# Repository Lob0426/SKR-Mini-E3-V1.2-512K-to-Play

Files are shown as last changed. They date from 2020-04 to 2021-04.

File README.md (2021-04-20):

# SKR-Mini-E3-V1.2-512K-to-Play
SKR Mini E3 V1.2 firmware for Printrbot Play w/o heated Bed (12/20/20)
This Firmware is used at your own risk.
This is for a Printrbot Play without heated Bed and has 3 point leveling for the induction probe. It has features set such as S_CURVE, LIN_ADV and ARC support.
It is set for the default size of 102mm X 102mm X 131
The SKR Mini5.stl is the one I finally used. It is a printable adapter plate from printrboard to SKR MINI. It orients the board 90degrees to the original board position. It lines the MicrSD on the board with the SD port in the Play chassis. This allowed me to use a Stock "CR10" LCD display where you need to use the onboard SD card to load files. The recommended TFT displays have USB and SD ports on them so this is not necessary to do for them. For the TFT displays you can use SKR Mini3.stl, but if you want to update firmware you will have to find a way to get to the MicroSD onboard to carry out that update. I recommend using the SKR Mini5.stl!

Board:
The Bigtreetech SKR Mini E3 Mini V1.2 board This board was designed as a direct replacement part for the Creality Ender 3 series of 3D Printers. It's size and layout match the Creality 1.1.4 and Creality 1.1.5 boards plus add extra connectors for TFT, NEOPixel, Filament runout sensor, BLTouch (servo connector), and extra fans
Specifications: Size: 100mm * 70.25mm
ARM Cortex-M3 CPU @ 75Mhz 256Kb documented available Flash (512 undocumented), 48K RAM.
Voltage: 12v or 24V operation depending on PSU, Hotend and Heated Bed unit used.
Drivers: Integrated TMC2209 drivers UART mode
Motor drive interfaces: X Axis, Y Axis, Z Axis, Extruder 0 (single extruder board)
Temperature Sensor interface: TH0, THB, 2 channel 100K NTC (thermal resistance)
Displays supported: 2.8"TFT, 3.5"TFT, Ender 3 original (CR10 display) LCD 12864 display
PC Communication interface: Mini USB type B @ 115200baud
File format: G-code
Recommended software: CURA, Simplify3D, Pronterface, Repetier-host, Makerware.

1/5/21 Added a BTT TFT35 E3 V3.0 Touchscreen to the Play. This allows you to usea USB stick or a full size SD card print instead. Makes the Play a whole lot easier to use. But the adapter board allows you to also use the Bords MicroSD card as well.

Connectors:
Connector type; JST-XH 2.54mm : Example: JST-XH connector set on Amazon
The Connectors on Printrbots are Molex(white) and Dupont(Black). To switch over to the SKR boards these have to be replaced or adapted to JST-XH connectors.
The Adaptrboard set adapts the Printrbot connectors to the SKR. They are a set of boards with incoming and outgoing terminals. The outgoing side plugs in from the Printrbot appropriate components plugs (X axis, Y axis, Z axis, Hotend etc.). The incoming side is to the SKR board you chose. The incoming side has short extensions (100mm about 4") between the SKR board and the Adaptrboards.
Manually replace the Molex and Dupont connectors with JST-XH connectors by cutting, stripping and crimping wires. 27 to 29 (1 fan, the hotend and the heated bed go into screw block and just need cutting and stripping) wires depending on whether you have a heated bed or not. Plus more if you have LEDS, NEOPixel, extra switches.
Another method would be to buy JST-XH 2.54mm Male wired cable connectors. Then cut, strip and solder and cover with shrink tube. This is probably as time consuming as crimping in the end. For some this is easier than crimping all those small pins to wires.

Of all these methods the cheapest is to crimp your own, the easiest is to buy the Adaptrboards and the most expensive is to solder them up. The Adaptrboards also have the advantage in they address the induction probe without having to wire in additional components. But if you are in a hurry and want to upgrade now, these are your options.

The Play Probe mount "Play probe mount18mm6.stl" (added 1/13/21) is for an 18mm inductive probe. The 8mm detection distance allows you to use a Ender 3/5 style magnetic removeable bed. This allows you to get rid of the Blue tape or PEI sheet. I finished the mount and it was flipped over to grab farther up the probe for a better grip. The earlier versions were allowing the probe to slip up and cause hotend crashes and melting pits in the build surface. This mount allows the probe to fit under the stock hotend cover.

printrbot foot2.stl is taller foot pads printed from TPU to improve cooling.

Overall the Play conversion has made it easier to use, easier to adjust and way quieter. It is what we see in Modern 3D printers produced today. It also has added safety as it has thermal overrun protection and resume after power outage. 

For more information see the Wiki: https://github.com/Lob0426/SKR-Mini-E3-V1.2-512K-to-Play/wiki

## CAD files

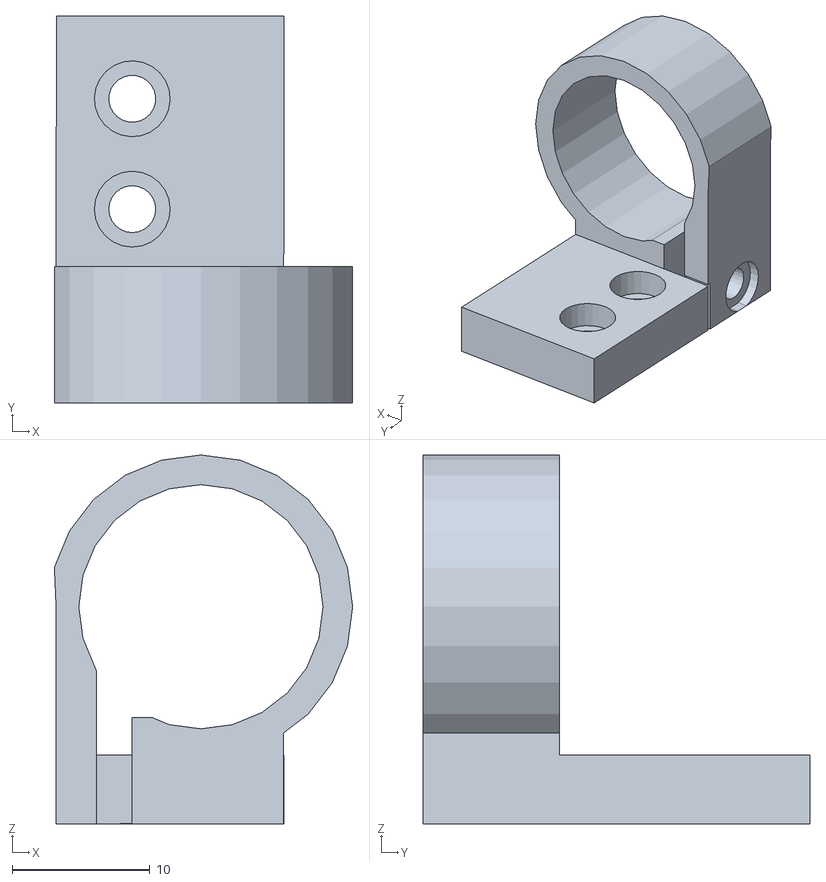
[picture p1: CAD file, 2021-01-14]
Play probe mount 18mm6.stl
21.6 x 28.1 x 26.8

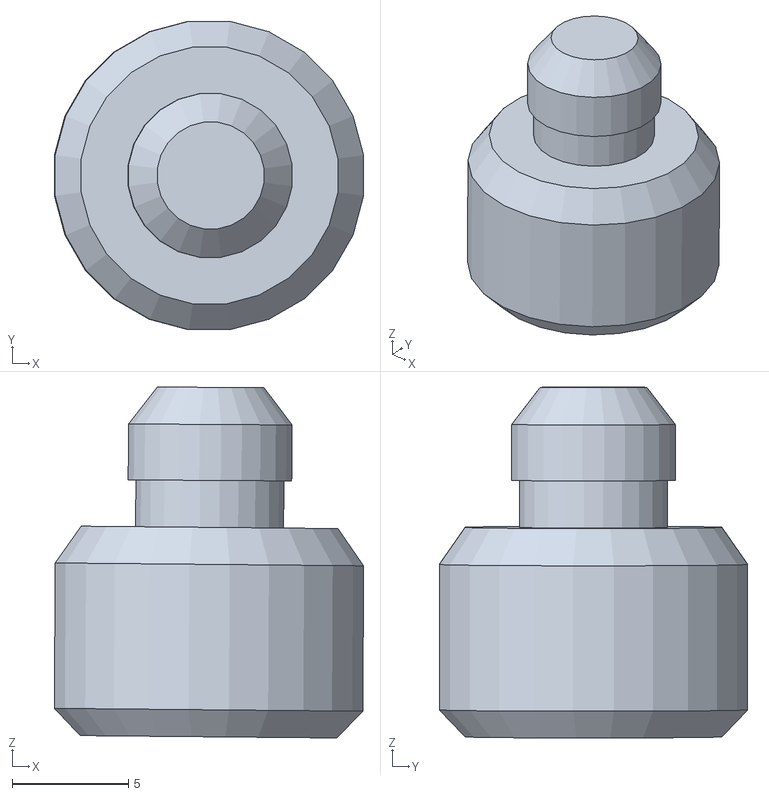
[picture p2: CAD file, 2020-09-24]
printrbot foot2.stl
13.3 x 13.3 x 15.1

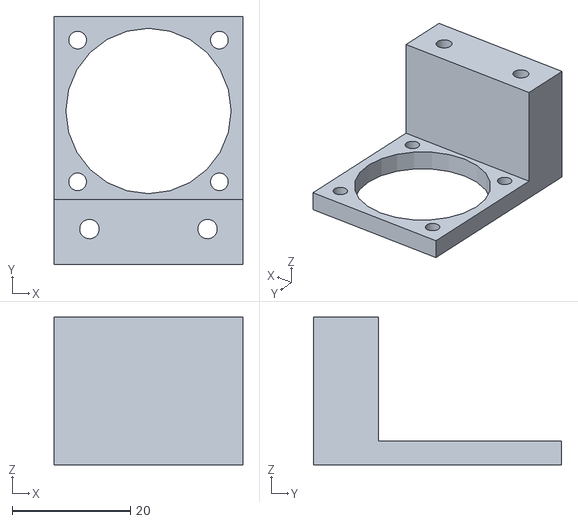
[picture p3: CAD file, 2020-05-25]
SKR fan mount2.stl
32.0 x 42.0 x 25.0

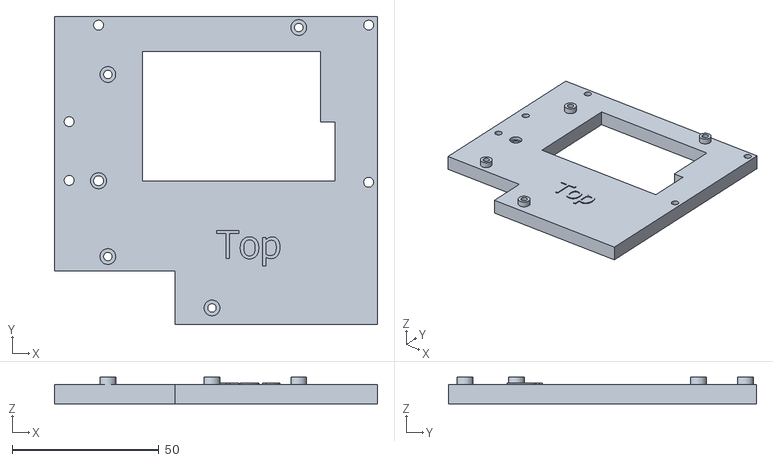
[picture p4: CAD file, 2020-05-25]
printrboard to SKR Mini5.stl
110.0 x 105.0 x 9.19

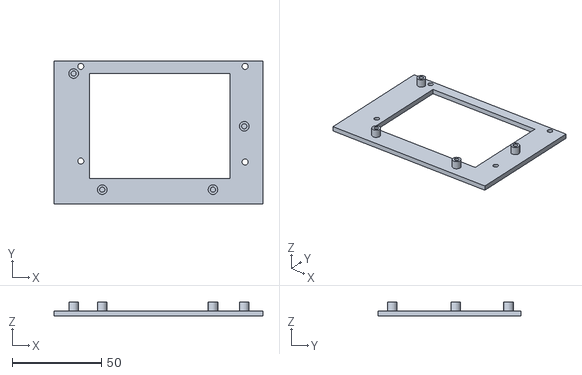
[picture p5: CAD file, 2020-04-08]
printrboard to SKR Mini3.stl
117.0 x 80.0 x 8.00

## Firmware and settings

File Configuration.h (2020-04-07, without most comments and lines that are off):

#pragma once
#define CONFIGURATION_H_VERSION 020000
#define STRING_CONFIG_H_AUTHOR "(BIGTREETECH, SKR-mini-E3-V1.2)" // Who made the changes.
#define SHOW_BOOTSCREEN
#define SERIAL_PORT 2
#define SERIAL_PORT_2 -1
#define BAUDRATE 115200
  #define MOTHERBOARD BOARD_BTT_SKR_MINI_E3_V1_2
#define CUSTOM_MACHINE_NAME "Printrbot Play"
#define EXTRUDERS 1
#define DEFAULT_NOMINAL_FILAMENT_DIA 1.75
#define TEMP_SENSOR_0 1
#define TEMP_SENSOR_1 0
#define TEMP_SENSOR_2 0
#define TEMP_SENSOR_3 0
#define TEMP_SENSOR_4 0
#define TEMP_SENSOR_5 0
#define TEMP_SENSOR_BED 5
#define TEMP_SENSOR_CHAMBER 0
#define DUMMY_THERMISTOR_998_VALUE 25
#define DUMMY_THERMISTOR_999_VALUE 100
#define MAX_REDUNDANT_TEMP_SENSOR_DIFF 10
#define TEMP_RESIDENCY_TIME     10  // (seconds) Time to wait for hotend to "settle" in M109
#define TEMP_WINDOW              1  // (°C) Temperature proximity for the "temperature reached" timer
#define TEMP_HYSTERESIS          3  // (°C) Temperature proximity considered "close enough" to the target
#define TEMP_BED_RESIDENCY_TIME 10  // (seconds) Time to wait for bed to "settle" in M190
#define TEMP_BED_WINDOW          1  // (°C) Temperature proximity for the "temperature reached" timer
#define TEMP_BED_HYSTERESIS      5  // (°C) Temperature proximity considered "close enough" to the target
#define HEATER_0_MINTEMP   3
#define HEATER_1_MINTEMP   5
#define HEATER_2_MINTEMP   5
#define HEATER_3_MINTEMP   5
#define HEATER_4_MINTEMP   5
#define HEATER_5_MINTEMP   5
#define BED_MINTEMP        3
#define HEATER_0_MAXTEMP 255
#define HEATER_1_MAXTEMP 275
#define HEATER_2_MAXTEMP 275
#define HEATER_3_MAXTEMP 275
#define HEATER_4_MAXTEMP 275
#define HEATER_5_MAXTEMP 275
#define BED_MAXTEMP      105
#define PIDTEMP
#define BANG_MAX 255     // Limits current to nozzle while in bang-bang mode; 255=full current
#define PID_MAX BANG_MAX // Limits current to nozzle while PID is active (see PID_FUNCTIONAL_RANGE below); 255=full current
#define PID_K1 0.95      // Smoothing factor within any PID loop
  #define PID_FUNCTIONAL_RANGE 10 // If the temperature difference between the target temperature and the actual temperature
  #define DEFAULT_Kp 40.15
  #define DEFAULT_Ki 7.10
  #define DEFAULT_Kd 56.73
#define MAX_BED_POWER 255 // limits duty cycle to bed; 255=full current
#define PREVENT_COLD_EXTRUSION
#define EXTRUDE_MINTEMP 170
#define PREVENT_LENGTHY_EXTRUDE
#define EXTRUDE_MAXLENGTH 600
#define THERMAL_PROTECTION_HOTENDS // Enable thermal protection for all extruders
#define THERMAL_PROTECTION_BED     // Enable thermal protection for the heated bed
#define THERMAL_PROTECTION_CHAMBER // Enable thermal protection for the heated chamber
#define USE_XMIN_PLUG
#define USE_ZMIN_PLUG
#define USE_YMAX_PLUG
#define ENDSTOPPULLUPS
#define X_MIN_ENDSTOP_INVERTING false // Set to true to invert the logic of the endstop.
#define Y_MIN_ENDSTOP_INVERTING false // Set to true to invert the logic of the endstop.
#define Z_MIN_ENDSTOP_INVERTING true // Set to true to invert the logic of the endstop.
#define X_MAX_ENDSTOP_INVERTING false // Set to true to invert the logic of the endstop.
#define Y_MAX_ENDSTOP_INVERTING false // Set to true to invert the logic of the endstop.
#define Z_MAX_ENDSTOP_INVERTING false // Set to true to invert the logic of the endstop.
#define Z_MIN_PROBE_ENDSTOP_INVERTING true // Set to true to invert the logic of the probe.
#define X_DRIVER_TYPE  TMC2209
#define Y_DRIVER_TYPE  TMC2209
#define Z_DRIVER_TYPE  TMC2209
#define E0_DRIVER_TYPE TMC2209
#define ENDSTOP_INTERRUPTS_FEATURE
#define DEFAULT_AXIS_STEPS_PER_UNIT   { 80, 80, 2020, 94.5 }
#define DEFAULT_MAX_FEEDRATE          { 300, 300, 7, 40 }
#define DEFAULT_MAX_ACCELERATION      { 2000, 2000, 100, 10000 }
#define DEFAULT_ACCELERATION          1500    // X, Y, Z and E acceleration for printing moves
#define DEFAULT_RETRACT_ACCELERATION  3000    // E acceleration for retracts
#define DEFAULT_TRAVEL_ACCELERATION   1500    // X, Y, Z acceleration for travel (non printing) moves
#define DEFAULT_EJERK    4.5  // May be used by Linear Advance
  #define JUNCTION_DEVIATION_MM 0.013  // (mm) Distance from real junction edge
#define S_CURVE_ACCELERATION
#define Z_MIN_PROBE_USES_Z_MIN_ENDSTOP_PIN
#define FIX_MOUNTED_PROBE
#define NOZZLE_TO_PROBE_OFFSET { 20, 0, 0 }
#define MIN_PROBE_EDGE 10
#define XY_PROBE_SPEED 7000
#define Z_PROBE_SPEED_FAST HOMING_FEEDRATE_Z
#define Z_PROBE_SPEED_SLOW (Z_PROBE_SPEED_FAST / 4)
#define MULTIPLE_PROBING 2
#define Z_CLEARANCE_DEPLOY_PROBE   4 // Z Clearance for Deploy/Stow
#define Z_CLEARANCE_BETWEEN_PROBES  3 // Z Clearance between probe points
#define Z_CLEARANCE_MULTI_PROBE     3 // Z Clearance between multiple probes
#define Z_PROBE_LOW_POINT          -2 // Farthest distance below the trigger-point to go before stopping
#define Z_PROBE_OFFSET_RANGE_MIN -4
#define Z_PROBE_OFFSET_RANGE_MAX 20
#define X_ENABLE_ON 0
#define Y_ENABLE_ON 0
#define Z_ENABLE_ON 0
#define E_ENABLE_ON 0 // For all extruders
#define DISABLE_X false
#define DISABLE_Y false
#define DISABLE_Z false
#define DISABLE_E false             // For all extruders
#define INVERT_X_DIR true
#define INVERT_Y_DIR true
#define INVERT_Z_DIR false
#define INVERT_E0_DIR false
#define INVERT_E1_DIR false
#define INVERT_E2_DIR false
#define INVERT_E3_DIR false
#define INVERT_E4_DIR false
#define INVERT_E5_DIR false
#define X_HOME_DIR -1
#define Y_HOME_DIR 1
#define Z_HOME_DIR -1
#define X_BED_SIZE 104
#define Y_BED_SIZE 195
#define X_MIN_POS 0
#define Y_MIN_POS 0
#define Z_MIN_POS 0
#define X_MAX_POS X_BED_SIZE
#define Y_MAX_POS Y_BED_SIZE
#define Z_MAX_POS 130
#define MIN_SOFTWARE_ENDSTOPS
  #define MIN_SOFTWARE_ENDSTOP_X
  #define MIN_SOFTWARE_ENDSTOP_Y
  #define MIN_SOFTWARE_ENDSTOP_Z
#define MAX_SOFTWARE_ENDSTOPS
  #define MAX_SOFTWARE_ENDSTOP_X
  #define MAX_SOFTWARE_ENDSTOP_Y
  #define MAX_SOFTWARE_ENDSTOP_Z
#define AUTO_BED_LEVELING_3POINT
#define MESH_BED_LEVELING
#define RESTORE_LEVELING_AFTER_G28
  #define ENABLE_LEVELING_FADE_HEIGHT
  #define SEGMENT_LEVELED_MOVES
  #define LEVELED_SEGMENT_LENGTH 5.0 // (mm) Length of all segments (except the last one)
  #define MESH_INSET 10          // Set Mesh bounds as an inset region of the bed
  #define GRID_MAX_POINTS_X 3    // Don't use more than 7 points per axis, implementation limited.
  #define GRID_MAX_POINTS_Y GRID_MAX_POINTS_X
#define LCD_BED_LEVELING
  #define MESH_EDIT_Z_STEP  0.025 // (mm) Step size while manually probing Z axis.
  #define LCD_PROBE_Z_RANGE 4     // (mm) Z Range centered on Z_MIN_POS for LCD Z adjustment
  #define MESH_EDIT_MENU        // Add a menu to edit mesh points
#define LEVEL_BED_CORNERS
  #define LEVEL_CORNERS_INSET 30    // (mm) An inset for corner leveling
  #define LEVEL_CORNERS_Z_HOP  4.0  // (mm) Move nozzle up before moving between corners
  #define LEVEL_CORNERS_HEIGHT 0.0  // (mm) Z height of nozzle at leveling points
#define Z_SAFE_HOMING
  #define Z_SAFE_HOMING_X_POINT ((X_BED_SIZE) / 2)    // X point for Z homing when homing all axes (G28).
  #define Z_SAFE_HOMING_Y_POINT ((Y_BED_SIZE) / 2)    // Y point for Z homing when homing all axes (G28).
#define HOMING_FEEDRATE_XY (50*60)
#define HOMING_FEEDRATE_Z  (4*60)
#define VALIDATE_HOMING_ENDSTOPS
#define EEPROM_SETTINGS       // Persistent storage with M500 and M501
#define EEPROM_CHITCHAT       // Give feedback on EEPROM commands. Disable to save PROGMEM.
  #define EEPROM_AUTO_INIT  // Init EEPROM automatically on any errors.
#define HOST_KEEPALIVE_FEATURE        // Disable this if your host doesn't like keepalive messages
#define DEFAULT_KEEPALIVE_INTERVAL 2  // Number of seconds between "busy" messages. Set with M113.
#define BUSY_WHILE_HEATING            // Some hosts require "busy" messages even during heating
#define PREHEAT_1_LABEL       "PLA"
#define PREHEAT_1_TEMP_HOTEND 190
#define PREHEAT_1_TEMP_BED     50
#define PREHEAT_1_FAN_SPEED   0 // Value from 0 to 255
#define PREHEAT_2_LABEL       "ABS"
#define PREHEAT_2_TEMP_HOTEND 230
#define PREHEAT_2_TEMP_BED    80
#define PREHEAT_2_FAN_SPEED   0 // Value from 0 to 255
#define PRINTJOB_TIMER_AUTOSTART
#define PRINTCOUNTER
#define LCD_LANGUAGE en
#define DISPLAY_CHARSET_HD44780 WESTERN
#define LCD_INFO_SCREEN_STYLE 0
#define SDSUPPORT
#define SD_CHECK_AND_RETRY
#define INDIVIDUAL_AXIS_HOMING_MENU
#define CR10_STOCKDISPLAY
#define SOFT_PWM_SCALE 0
#define SERVO_DELAY { 300 }

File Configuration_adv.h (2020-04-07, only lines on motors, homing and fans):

#define E0_AUTO_FAN_PIN -1
#define E1_AUTO_FAN_PIN -1
#define E2_AUTO_FAN_PIN -1
#define E3_AUTO_FAN_PIN -1
#define E4_AUTO_FAN_PIN -1
#define E5_AUTO_FAN_PIN -1
#define CHAMBER_AUTO_FAN_PIN -1
#define X_HOME_BUMP_MM 0
#define Y_HOME_BUMP_MM 0
#define Z_HOME_BUMP_MM 2
#define HOMING_BUMP_DIVISOR { 2, 2, 4 }  // Re-Bump Speed Divisor (Divides the Homing Feedrate)
#define QUICK_HOME                       // If homing includes X and Y, do a diagonal move initially
#define HOMING_BACKOFF_MM { 2, 2, 2 }  // (mm) Move away from the endstops after homing
#define MICROSTEP_MODES { 16, 16, 16, 16, 16, 16 } // [1,2,4,8,16]
#define DIGIPOT_I2C_MOTOR_CURRENTS { 1.0, 1.0, 1.0, 1.0, 1.0, 1.0, 1.0, 1.0 }  //  AZTEEG_X3_PRO
#define LIN_ADVANCE
  #define LIN_ADVANCE_K 0.0    // Unit: mm compression per 1mm/s extruder speed
#define ADVANCED_PAUSE_FEATURE
  #define ADVANCED_PAUSE_PURGE_FEEDRATE        3  // (mm/s) Extrude feedrate (after loading). Should be slower than load feedrate.
  #define ADVANCED_PAUSE_PURGE_LENGTH         50  // (mm) Length to extrude after loading.
  #define ADVANCED_PAUSE_RESUME_PRIME          0  // (mm) Extra distance to prime nozzle after returning from park.
    #define X_CURRENT       800        // (mA) RMS current. Multiply by 1.414 for peak current.
    #define X_CURRENT_HOME  X_CURRENT  // (mA) RMS current for sensorless homing
    #define X_MICROSTEPS     16    // 0..256
    #define Y_CURRENT       800
    #define Y_CURRENT_HOME  Y_CURRENT
    #define Y_MICROSTEPS     16
    #define Z_CURRENT       800
    #define Z_CURRENT_HOME  Z_CURRENT
    #define Z_MICROSTEPS     16
    #define E0_CURRENT      800
    #define E0_MICROSTEPS    16
  #define X_HYBRID_THRESHOLD     100  // [mm/s]
  #define X2_HYBRID_THRESHOLD    100
  #define Y_HYBRID_THRESHOLD     100
  #define Y2_HYBRID_THRESHOLD    100
  #define Z_HYBRID_THRESHOLD       3
  #define Z2_HYBRID_THRESHOLD      3
  #define Z3_HYBRID_THRESHOLD      3
  #define E0_HYBRID_THRESHOLD     30
  #define E1_HYBRID_THRESHOLD     30
  #define E2_HYBRID_THRESHOLD     30
  #define E3_HYBRID_THRESHOLD     30
  #define E4_HYBRID_THRESHOLD     30
  #define E5_HYBRID_THRESHOLD     30

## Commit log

2020-04-08 Create adapter to mount board
2020-05-07 Added b oard specs and connectors type
2020-05-25 updated board mount with fan mount
    [SKR fan mount2.stl, printrboard to SKR Mini5.stl]
2020-09-24 Added taller foot pad
    [printrbot foot2.stl]
2021-01-14 Delete Play probe mount4.stl
    NEWER FILE
    [Play probe mount4.stl]
2021-01-14 newer file
    [Play probe mount5.stl]
2021-01-14 Play 18mm probe stl
    [Play probe mount 18mm6.stl]
2021-01-16 Create Setting the probe and Z offset
2021-01-16 Update Setting the probe and Z offset

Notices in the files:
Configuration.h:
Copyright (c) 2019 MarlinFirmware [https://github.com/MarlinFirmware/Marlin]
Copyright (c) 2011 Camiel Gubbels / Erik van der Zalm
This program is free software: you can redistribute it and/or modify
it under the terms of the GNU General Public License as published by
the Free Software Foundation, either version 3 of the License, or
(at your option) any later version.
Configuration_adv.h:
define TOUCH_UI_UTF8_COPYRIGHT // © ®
